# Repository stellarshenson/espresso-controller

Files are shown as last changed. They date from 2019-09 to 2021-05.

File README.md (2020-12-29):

## Homekit Enabled Rancillio Espresso Controller ##
Homekit enabled Rancilio Espresso Controller for Rancilio Silvia v5 Espresso Machine

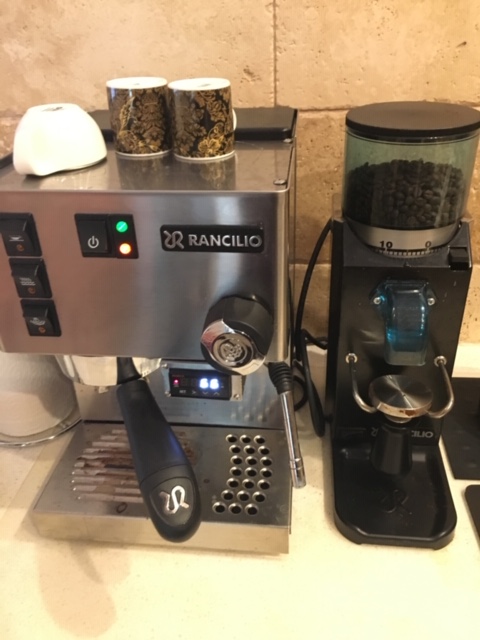
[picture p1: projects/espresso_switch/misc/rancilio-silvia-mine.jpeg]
rancilio silvia


this project was possible thanks to the freeRTOS and esp-open-sdk
Also thanks to folowing other projects:
* [maximkulkin/esp-homekit](https://github.com/maximkulkin/esp-homekit.git)
* [maximkulkin/esp-wifi-config](https://github.com/maximkulkin/esp-wifi-config)
* [ravensystem/esp-adv-button](https://github.com/RavenSystem/esp-adv-button.git)

This module is specifically designed to control turning on-and-off Rancilio Silvia v5 Espresso Machine.
Rancilio Silvia has only a momentary switch that while toggled, powers the machine on (when previously off) and off (when previously on).
Additionally Rancilio Silvia uses an internal timer that turns the machine off after 30min

Espresso Controller monitors the internal power state of the espresso machine and controls powering the machine up and down when activated

### Firmware Build ###
1. Clone the project. Next, initialize and sync all submodules (recursively):
```shell
git clone --recursive https://github.com/stellarshenson/espresso-controller.git
cd espresso-controller
git submodule update --init --recursive
```
2. Install [esp-open-sdk](https://github.com/pfalcon/esp-open-sdk), build it with `make toolchain esptool libhal STANDALONE=n`, then edit your PATH and add the generated toolchain bin directory. The path will be something like /path/to/esp-open-sdk/xtensa-lx106-elf/bin
3. Install [esptool.py](https://github.com/themadinventor/esptool) and make it available on your PATH. If you used esp-open-sdk then this is done already. Alternatively you can use the [NodeMCU flasher](https://github.com/nodemcu/nodemcu-flasher/tree/master/Win64/Release)
4. Checkout [esp-open-rtos](https://github.com/SuperHouse/esp-open-rtos) and set SDK_PATH environment variable pointing to it.
5. Build espresso_switch firmware:
```shell
make -C projects/espresso_switch suite
```
Files generated by the make script should be:
```shell
ls firmware
0x00000_rboot.bin  0x10000_blank_0x00_1M.bin  0x10000_blank_config.bin  0x20000_espresso_switch.bin
```
The prefix indicates where in the flash the firmware should be burned, use it when flashing with [esptool.py](https://github.com/themadinventor/esptool) or the [NodeMCU flasher](https://github.com/nodemcu/nodemcu-flasher/tree/master/Win64/Release). Additional settings for flashing of the firmware are: SPI Mode = DOUT, Baudrate = 230400, Flash size = <flash size of your Wemos unit in Mbyte>

### Principle of operation ###
The device is supposed to control the powering up and down the espresso machine and notify any power changes to the Homekit clients nearby. In the future the device will be able to control the auto-shutdown of the espresso machine (powersaving) and flushing (running water through the group after warm-up). Additionally the firmware will monitor the boiler temperature in the future.

Currently the device extends the following number of output interfaces:
* __Toggle interface__ - controls the toggle switch and works exactly like the momentary switch on the espresso machine front panel
* __Power sense interface__ - senses whether the machine is on or off (and provides notifications to the homekit clients)
* __Status LED__ - indicates the status of the device, fast blink = booting up, slow-blink = AP mode, no blink = connected to the network, SOS blink (3 short, 3 long, 3 short) = problem
* __Button__ - press once to manually trigger power switch (used to test device wiring). hold for 10s to reset device to factory settings

Additionally, when connected through the microUSB port to the computer, the device outputs serial diagnostics messages and extends serial commandline. Type *help* to get the list of available commands.

The serial inteface was configured with the __74880 baud rate__

### Functionality ###
Device boots up in 2 different modes:
1. as new device, you need to find its wifi ssid (Espresso-Switch-xxxx) and configure its access to your network via web captive portal
2. as connected device. you need to connect to its IP and capture its Homekit code
3. as homekit device. it is ready for operation once added to your homekit network

### Typical Circuit Layout ###
You would need the following parts to complete the build
* __Wemos D1 Mini <any>__ - any wemos with 4Mb+ flash works (Mini or Mini Pro)
* __Optocoupler + 1k Resistor (D6)__ - used for powersense. The Rancilio Silvia 12V power indicator circuit it very noisy, we would use the optocoupler to provide galvanic isolation between the controller and the espresso machine
* __Relay__ (3.3V level or Relay 5v + NPN transistor and a couple of passive jellybeans) - this needs to switch the 12v AC momentary switch
* __1 Status LED + 330 Resistor__ - this is just a status LED. Fast blink = starting up, Slow blink - AP mode, No blink - connected to network 
* __HI-Link 5V power module__ (to power the thing up from mains) - it would be preferred to connect the controller to the mains terminals at the Rancilio power brick. I am figuiring out other options, stay tuned. Voltage for the Wemos D1 must be relatively clean.Wemos has onboard a small 3v3 linear power supply controller. Please keep in mind that Wemos D1 uses 3v3 logic levels :-)

I will publish the full BOM as soon as I finish the PCB build and installation

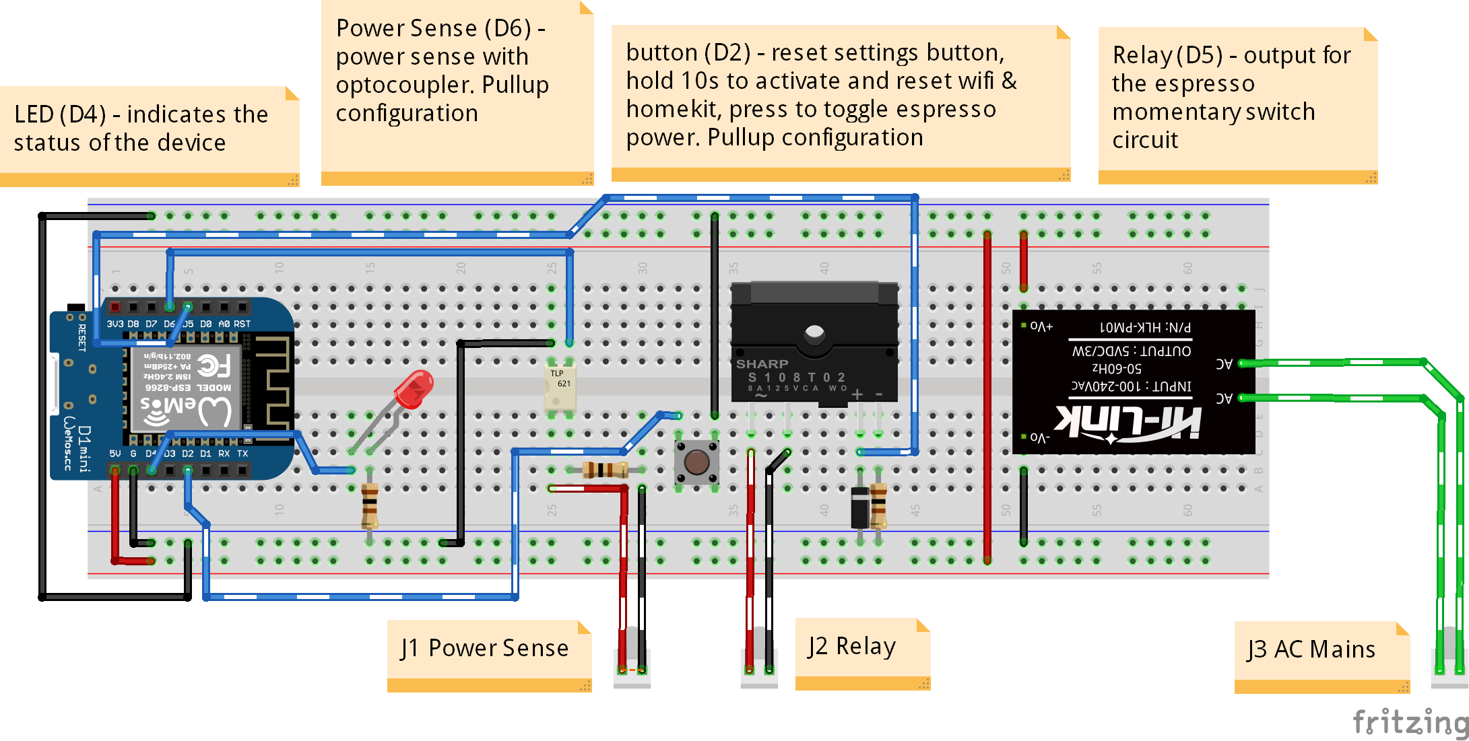
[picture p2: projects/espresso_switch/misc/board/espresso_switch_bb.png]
circuit layout

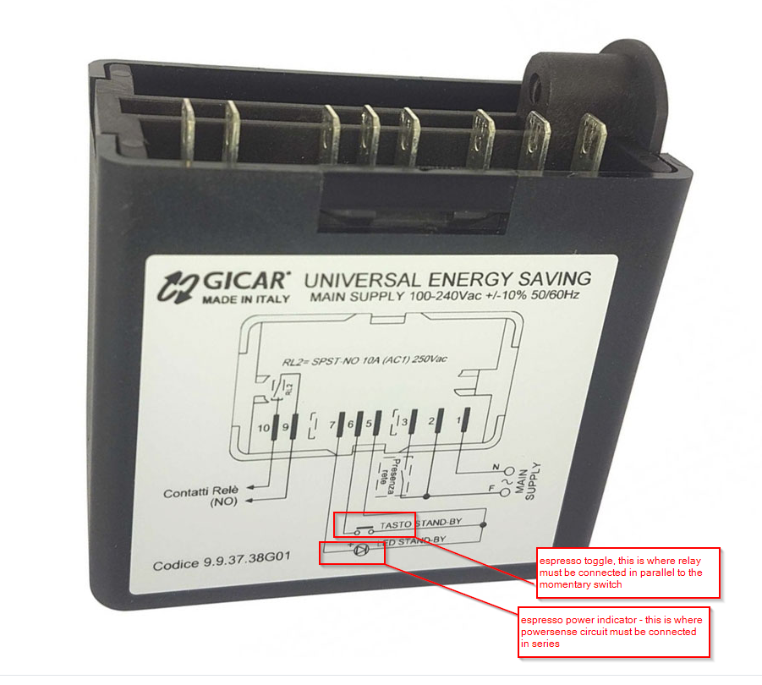
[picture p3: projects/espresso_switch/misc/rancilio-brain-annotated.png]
power brick


## Circuit and PCB ##
All schematics and PCB files are available in the [misc/board](https://github.com/stellarshenson/espresso-controller/blob/master/projects/espresso_switch/misc/board) directory. The bill of materials is up-to-date in the [schematics pdf](https://github.com/stellarshenson/espresso-controller/blob/master/projects/espresso_switch/misc/board/espresso_switch_schematics.pdf)

PCB design is for one-sided PCB with a copper pour connected to the GND. [PCB printout](https://github.com/stellarshenson/espresso-controller/blob/master/projects/espresso_switch/misc/board/espresso_switch_pcb_bottom.pdf) printout available as 600dpi to print and etch according to [instructions](https://github.com/stellarshenson/espresso-controller/blob/master/projects/espresso_switch/misc/board/pcb_howto.txt). Schematics and PCB files were produced with DipTrace

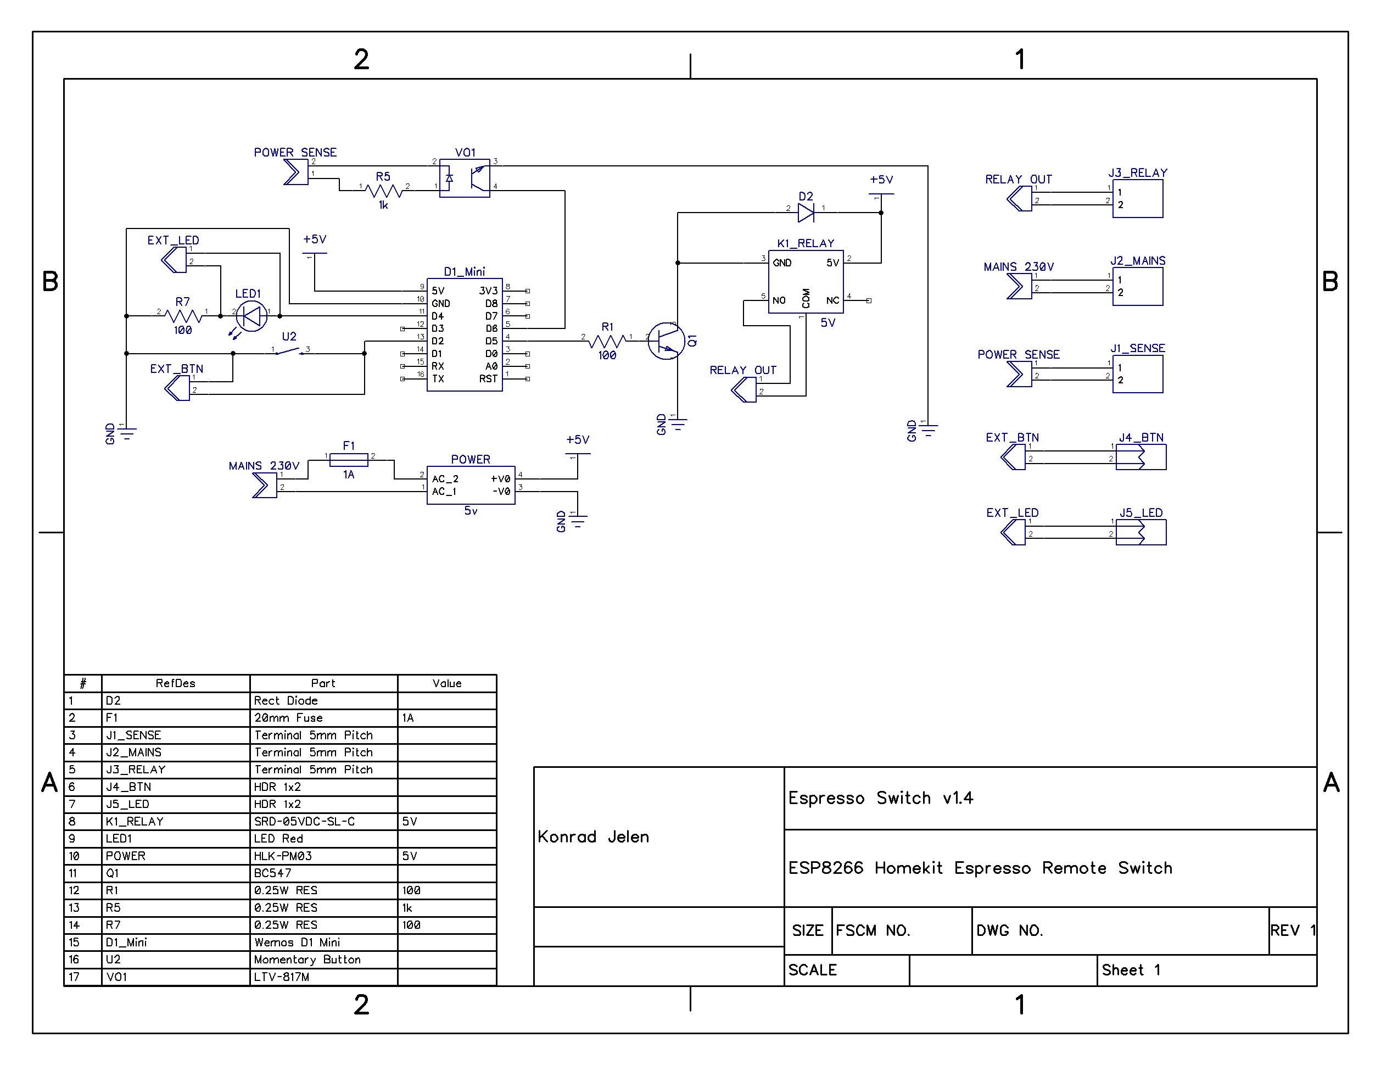
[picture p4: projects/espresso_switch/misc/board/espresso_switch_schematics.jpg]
circuit

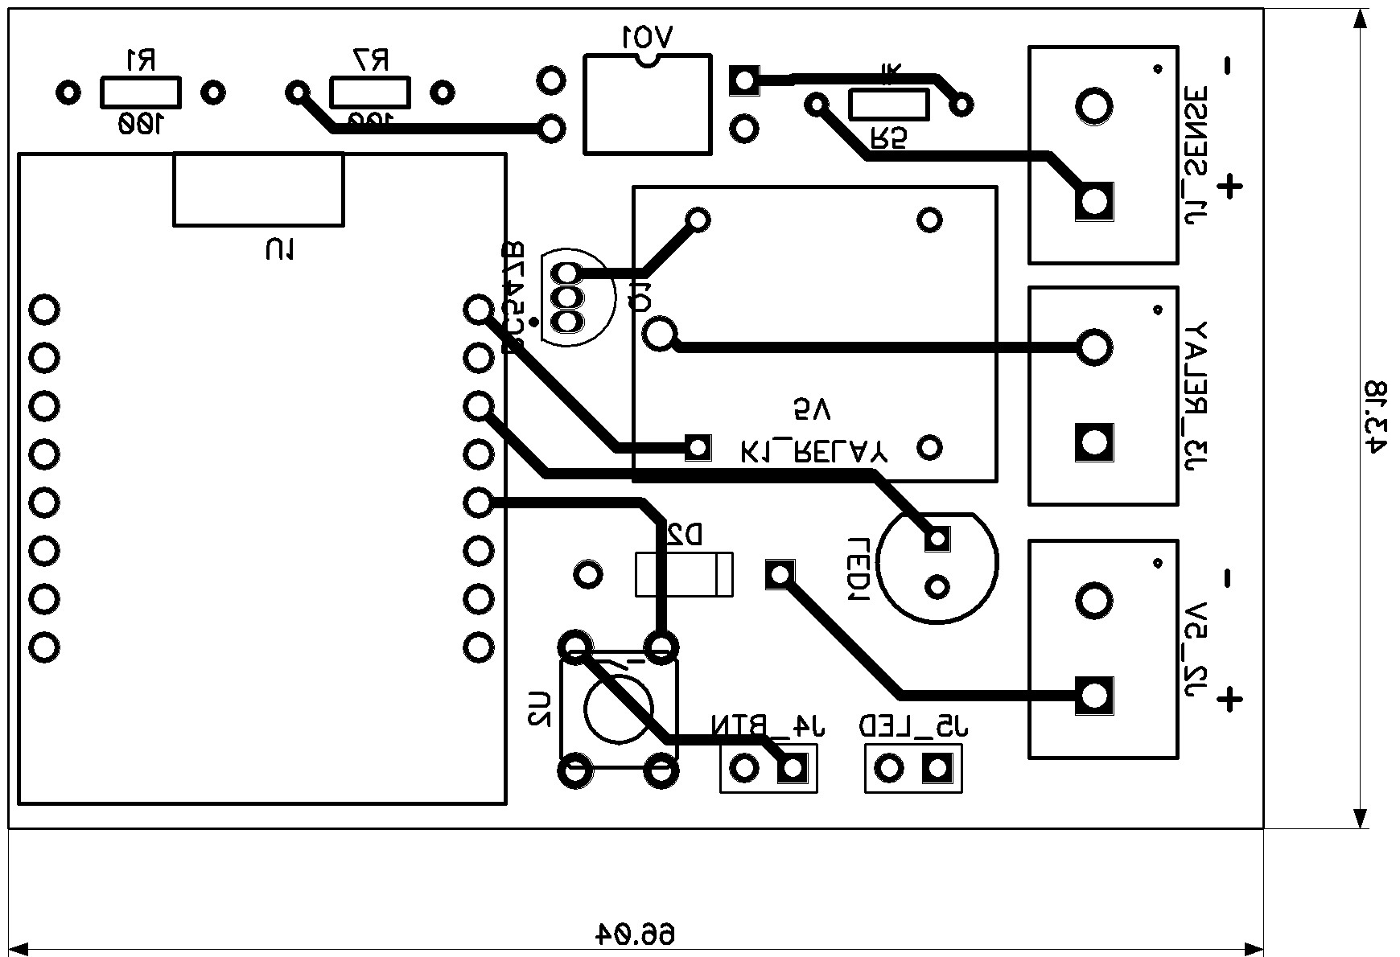
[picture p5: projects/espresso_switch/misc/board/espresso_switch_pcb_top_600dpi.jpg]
pcb top

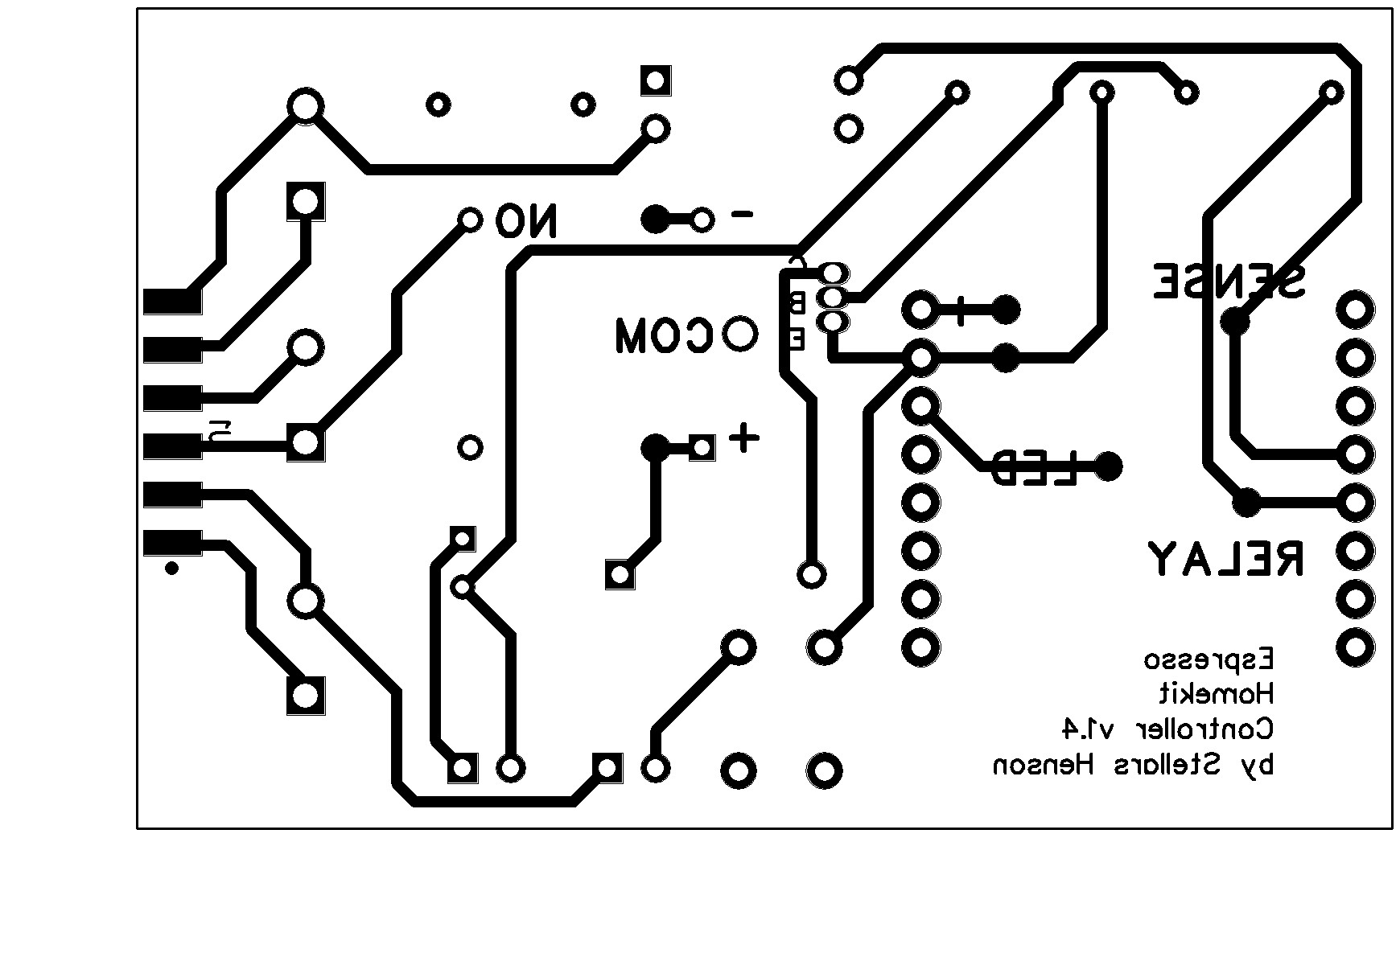
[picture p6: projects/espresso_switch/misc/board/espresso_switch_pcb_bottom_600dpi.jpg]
pcb bottom


### Installation ###
TBD

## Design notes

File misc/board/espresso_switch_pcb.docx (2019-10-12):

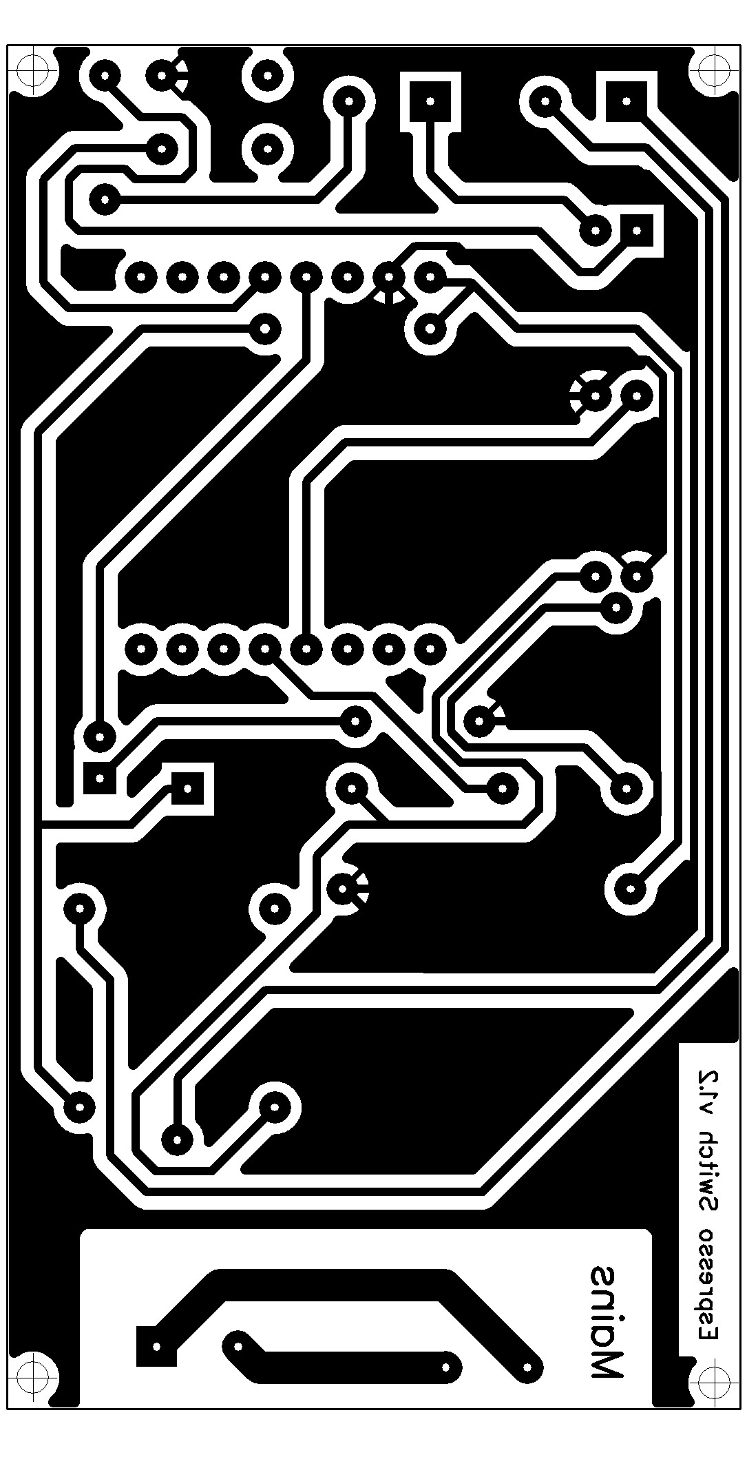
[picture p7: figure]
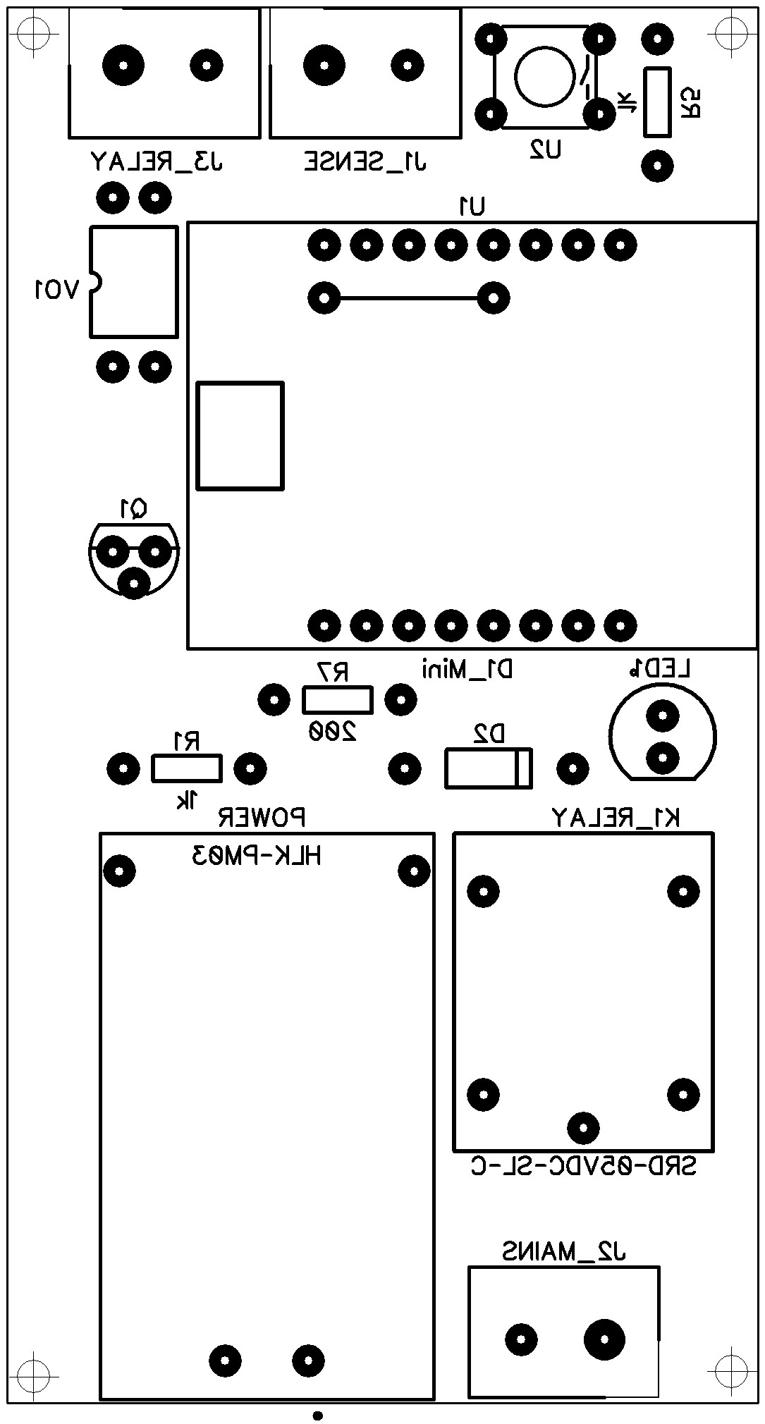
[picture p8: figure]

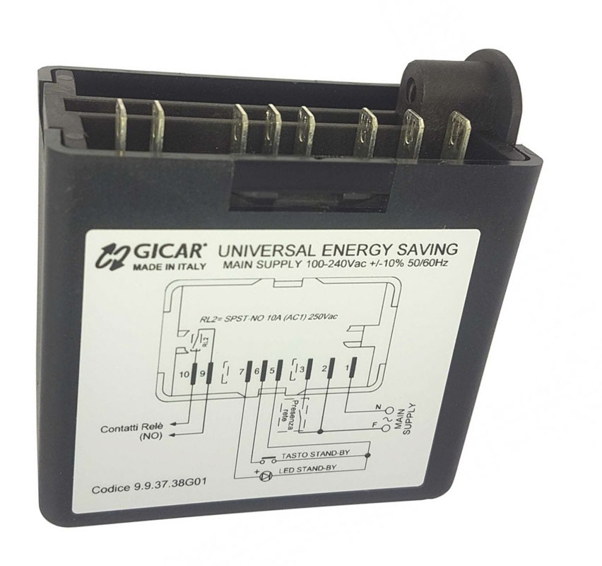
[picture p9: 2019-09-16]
misc/rancilio-brain-1.jpeg

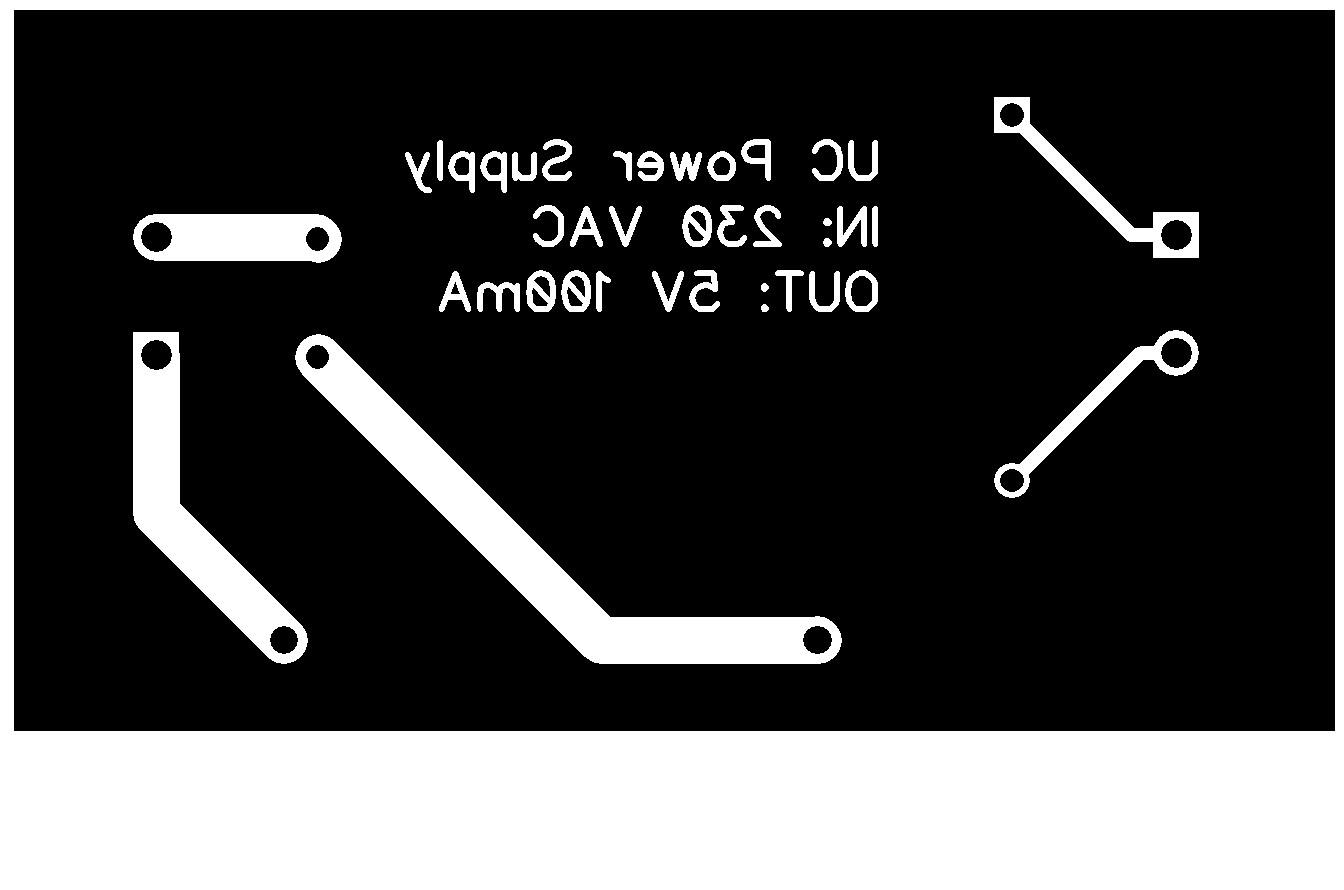
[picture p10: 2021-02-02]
misc/board/espresso_switch_power_supply_fused_bottom_600dpi.jpg

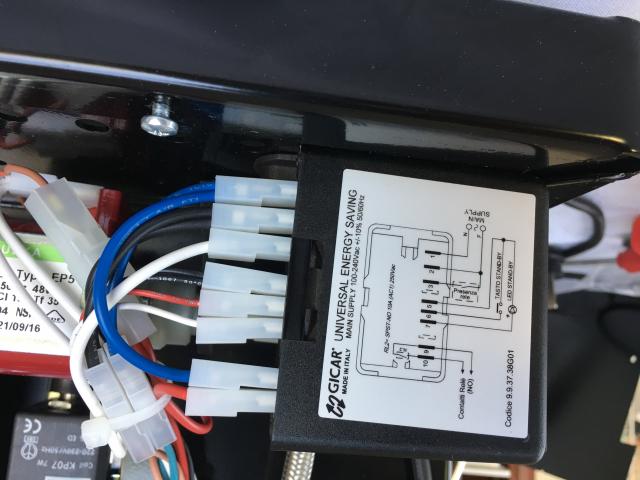
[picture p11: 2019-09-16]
misc/rancilio-brain-2.jpeg

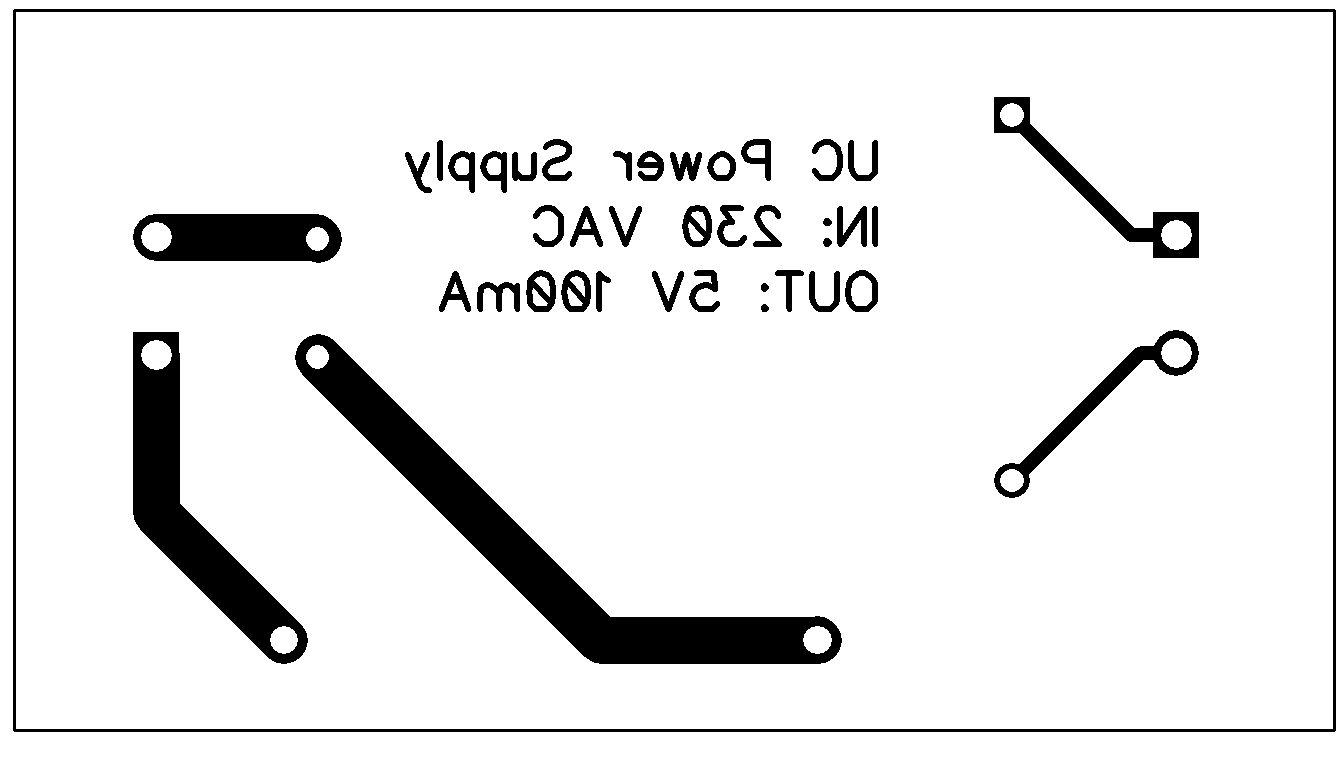
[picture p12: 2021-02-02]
misc/board/espresso_switch_pcb_bottom_600dpi.bmp

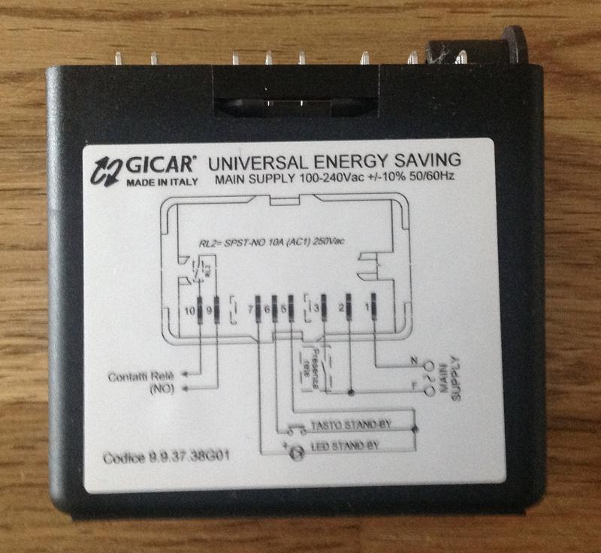
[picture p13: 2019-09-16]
misc/rancilio-brain.jpeg

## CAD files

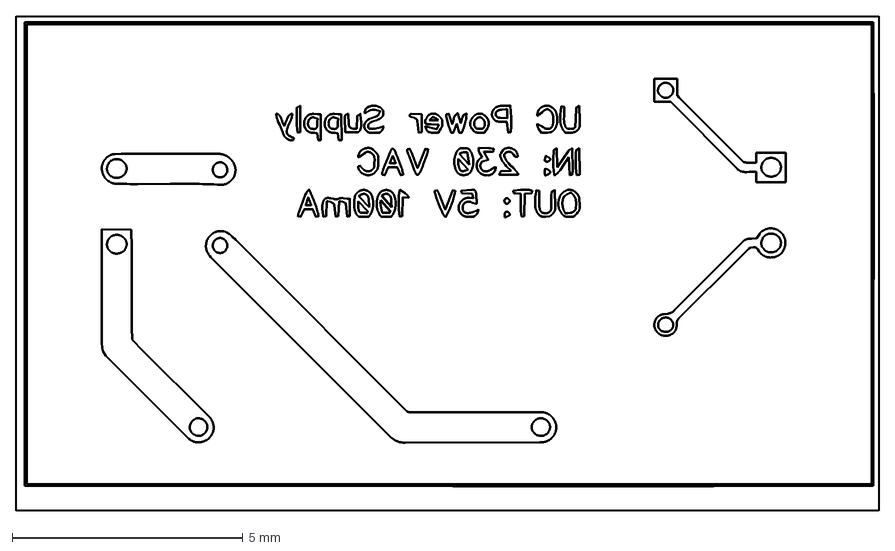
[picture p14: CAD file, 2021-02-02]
misc/board/espresso_switch_pcb_bottom_600dpi.dxf
18.7 x 10.7 mm

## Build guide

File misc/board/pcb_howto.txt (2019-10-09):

1. paste 400dpi or 600dpi bmp-s in the MS word document
2. change placement type to "background picture"
3. change picture scale to 24% (400dpi) or 16% (600dpi)

the printout should be of correct size after that

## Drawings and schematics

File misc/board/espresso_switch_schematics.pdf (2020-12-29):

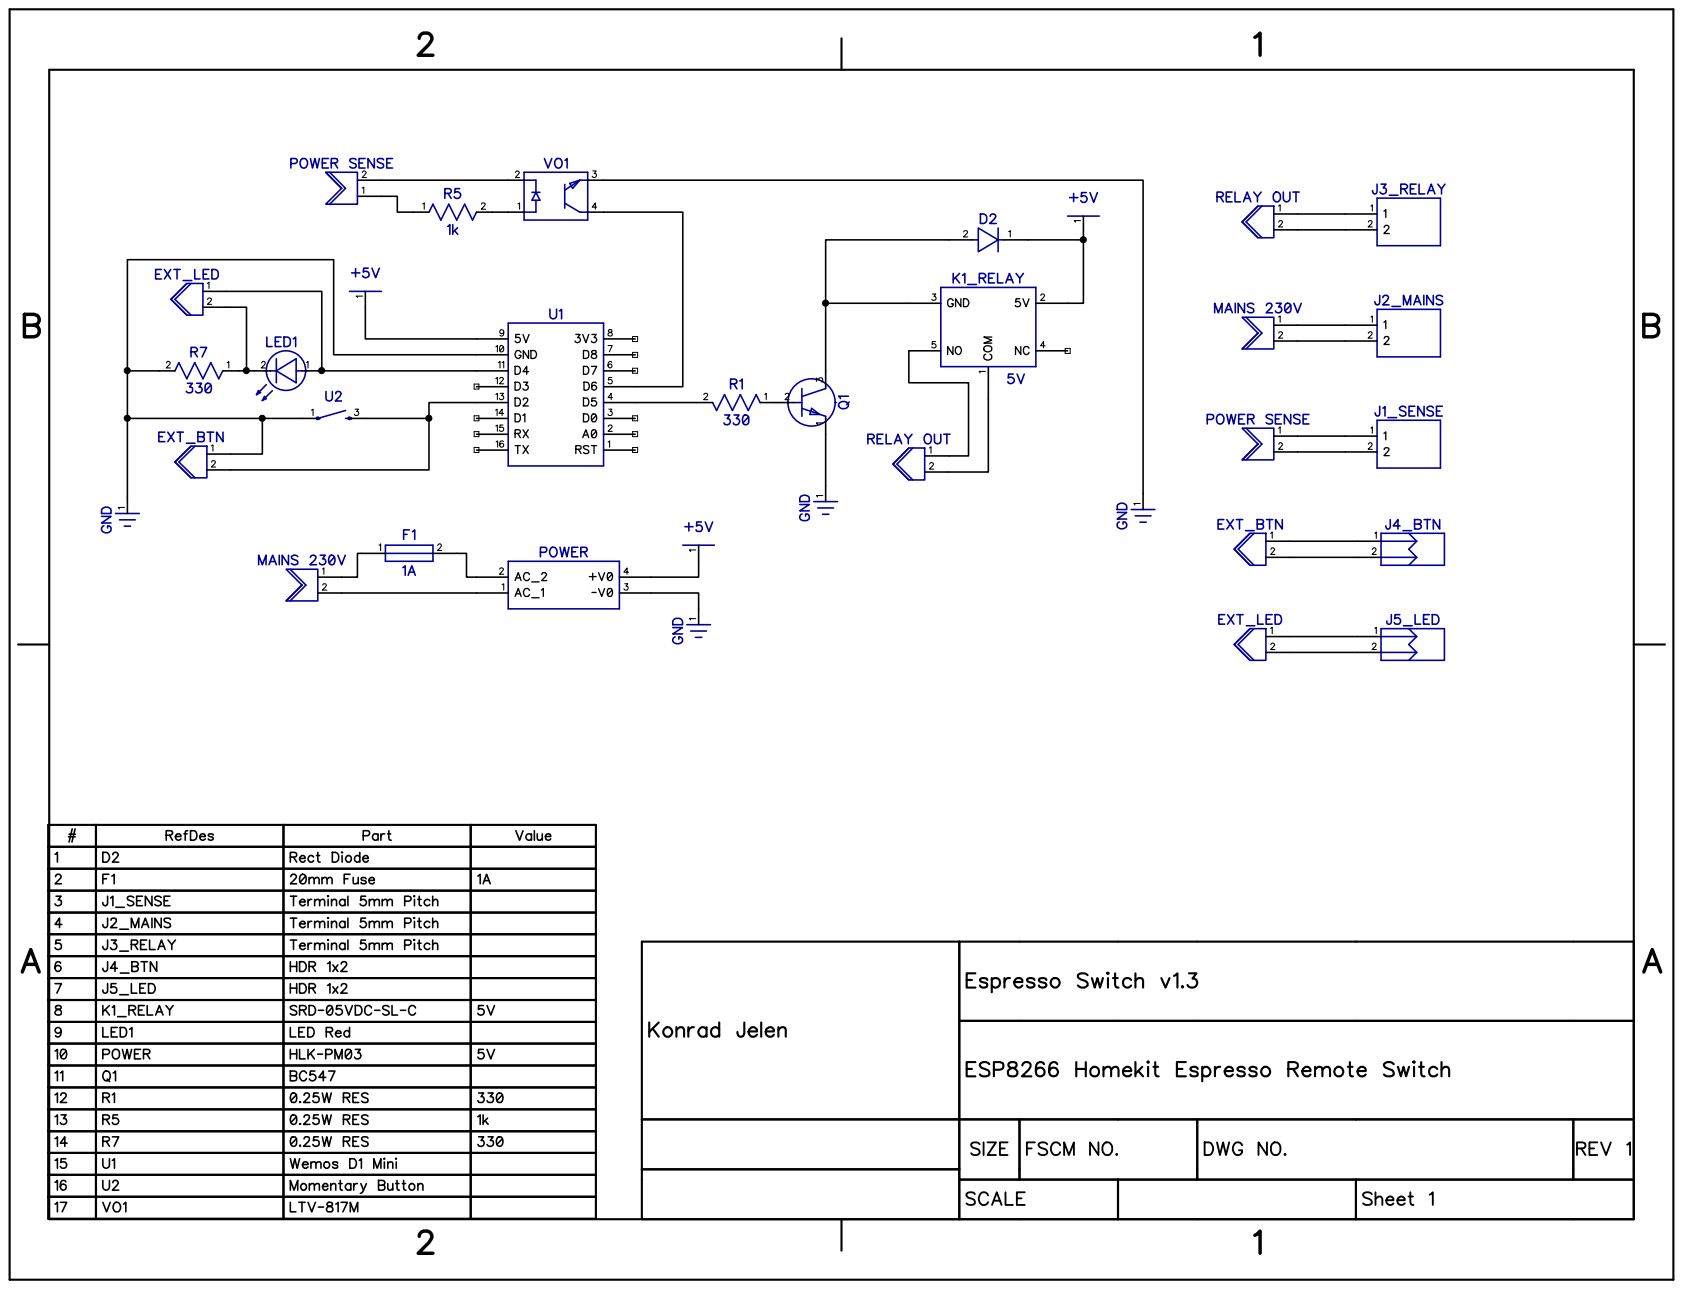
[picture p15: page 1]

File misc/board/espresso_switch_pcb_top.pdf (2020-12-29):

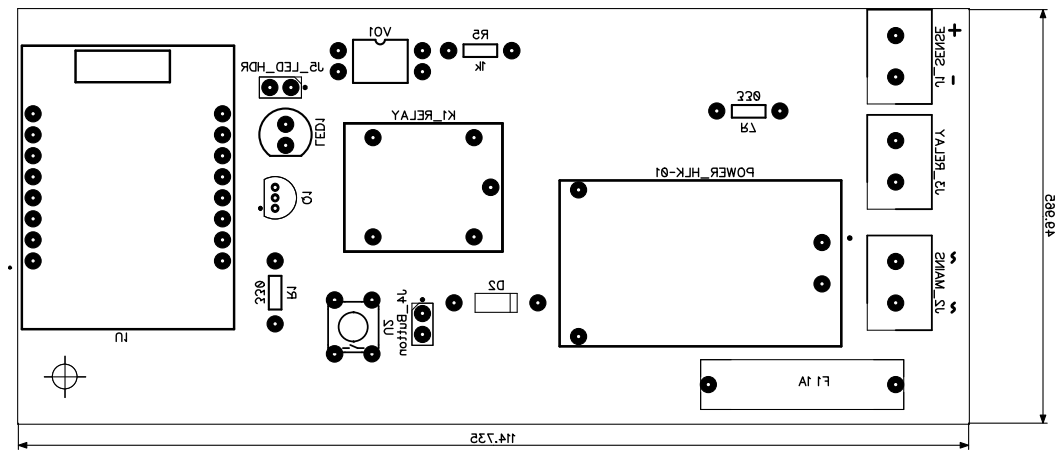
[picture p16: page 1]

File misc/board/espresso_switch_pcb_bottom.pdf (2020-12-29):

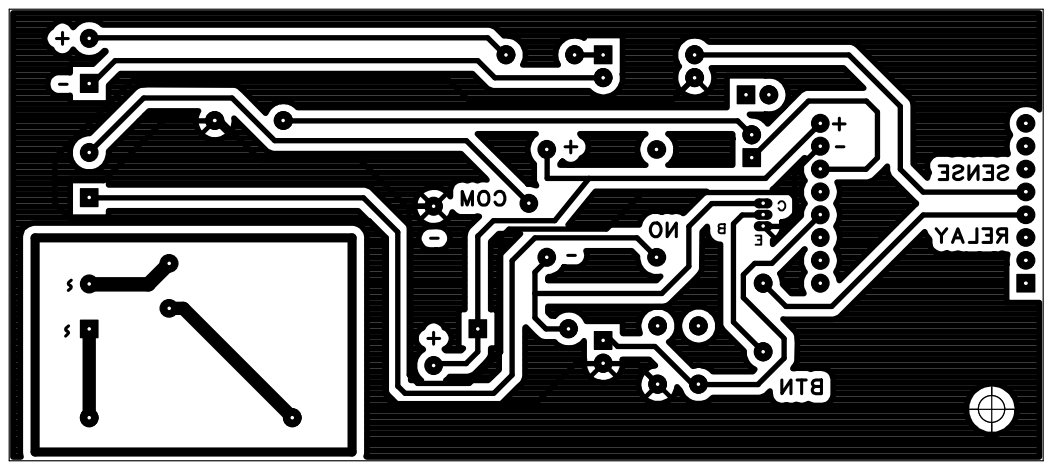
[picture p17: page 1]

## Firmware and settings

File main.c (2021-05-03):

/*
 *
 * Espresso controller accessory where On/Of functions
 * by toggling monostable switch and looks at the SENSE
 * pin to find if espresso machine is on
 *
 * This accessory uses the modified wifi-config library
 * that has the homekit id generated from the chipid and
 * starts an AP mode with a HTTP server upon start when
 * wifi config was found.
 *
 * After successful connection accessory shuts down AP.
 * 
 *  Wemos D1 Mini Pro
 *
 *                 RST -|         |- TX  / GPIO1
 *           ADC0 / A0 -|         |- RX  / GPIO3
 *  D0 / WAKE / GPIO16 -|         |- D1 / SCL / GPIO5
 *  D5 / SCLK / GPIO14 -|         |- D2 / SDA / GPIO4
 *  D6 / MISO / GPIO12 -|         |- D3 / FLASH / GPIO0
 *  D7 / MOSI / GPIO13 -|         |- D4 / GPIO2 / Onboard LED
 *  D8 / CS /   GPIO15 -|   USB   |- GND
 *                 3V3 -|___|=|___|- 5V
 */

#include <stdio.h>
#include <stdlib.h>
#include <esp/uart.h>
#include <esp8266.h>
#include <FreeRTOS.h>
#include <task.h>
#include <string.h>
#include <sysparam.h>

#include <serial-cmdline.h>
#include <led_status.h>

#include <homekit/homekit.h>
#include <homekit/characteristics.h>
#include <wifi_config.h>
#include <adv_button.h>
#include <espressif/esp_system.h>
#include <espressif/esp_common.h>
#include <esp/hwrand.h>


/* the following is for fetching the time over ntp protocol */
#include <sntp.h>
#include <time.h>

#ifndef PROTO_UUID
#define PROTO_UUID "-03a1-4971-92bf-af2b7d833922"
#endif

#ifndef UUID
#define UUID "01010101" PROTO_UUID
#endif

#define INFO(message, ...) printf(">>> " message "\n", ##__VA_ARGS__);
#define ERROR(message, ...) printf("!!! " message "\n", ##__VA_ARGS__);

#define GPIO_ESPRESSO_RELAY     14  // D5 = GPIO14
#define GPIO_STATUS_LED         2   // D3 = GPIO00, D4 = GPIO02
#define GPIO_ESPRESSO_SENSE     12  // D6 = GPIO12
#define GPIO_BUTTON             4   // D2 = GPIO04
#define ESPRESSO_SENSE_DELAY    1000
#define ESPRESSO_TOGGLE_TIME    500
#define SNTP_SYNC_PERIOD	5*60000	
#define SNTP_SERVERS		"0.pool.ntp.org", "1.pool.ntp.org", "2.pool.ntp.org", "3.pool.ntp.org"

#define DEFAULT_SWITCH_MODE	switch_mode_momentary

#define SYSPARAM_SWITCH_MODE		"switch_mode"
#define SYSPARAM_HOMEKIT_PASSWORD	"homekit_password"
#define SYSPARAM_BOOTSTRAPPED		"device_bootstrapped"


//pairing password to display, this will be embedded in the AP homepage
#define CUSTOM_HTML "<p><b>Espresso Switch Accessory </b><br> %s </p>"
#define INITIAL_ACCESSORY_PASSWORD "111-11-111"
#define HOMEKIT_SETUPID "1QJ8"

#define HOMEKIT_CUSTOM_UUID(value) (value PROTO_UUID)
#define HOMEKIT_SERVICE_CUSTOM_SETUP HOMEKIT_CUSTOM_UUID("F00000FF")
#define HOMEKIT_CHARACTERISTIC_CUSTOM_SHOW_SETUP HOMEKIT_CUSTOM_UUID("00000001")
#define HOMEKIT_DECLARE_CHARACTERISTIC_CUSTOM_SHOW_SETUP(_value, ...) \
    .type = HOMEKIT_CHARACTERISTIC_CUSTOM_SHOW_SETUP, \
    .description = "Show Setup", \
    .format = homekit_format_bool, \
    .permissions = homekit_permissions_paired_read \
    | homekit_permissions_paired_write \
    | homekit_permissions_notify, \
    .value = HOMEKIT_BOOL_(_value), \
    ##__VA_ARGS__


//prototypes
void espresso_on_callback(homekit_characteristic_t *_ch, homekit_value_t on, void *context);
void espresso_sense_task();
void espresso_toggle(bool _on);
void espresso_cycle();
void status_led_write(bool on);
void accessory_identify_task(void *_args);
void accessory_identify_callback(homekit_value_t _value);
void led_identify(homekit_value_t _value);
void show_setup_callback();
void serial_read_task();
void on_command(char* cmd);
void reset_settings();
void save_settings();
void espresso_status();

/*
 * declared characteristics:
 * espresson_on - controls espresso power
 * show_setup - controls whether custom setup visibility
 * */
homekit_characteristic_t espresso_on = HOMEKIT_CHARACTERISTIC_(ON, false, .callback=HOMEKIT_CHARACTERISTIC_CALLBACK(espresso_on_callback));
homekit_characteristic_t show_setup = HOMEKIT_CHARACTERISTIC_(CUSTOM_SHOW_SETUP, true, .callback=HOMEKIT_CHARACTERISTIC_CALLBACK(show_setup_callback));
//homekit_characteristic_t wifi_reset = HOMEKIT_CHARACTERISTIC_(CUSTOM_WIFI_RESET, false, .id=131, .callback=HOMEKIT_CHARACTERISTIC_CALLBACK(change_settings_callback));

// declare accessories / services and characteristics
// those are furhter initialised with homekit_server_init after wifi is configured
homekit_accessory_t *accessories[] = {
    //accessories
    HOMEKIT_ACCESSORY(.id=1, .category=homekit_accessory_category_lightbulb, .services=(homekit_service_t*[]){
	//servces - information
	HOMEKIT_SERVICE(ACCESSORY_INFORMATION, .characteristics=(homekit_characteristic_t*[]){
	    //characteristics
	    HOMEKIT_CHARACTERISTIC(NAME, "Espresso Switch"),
	    HOMEKIT_CHARACTERISTIC(MANUFACTURER, "Stellars"),
	    HOMEKIT_CHARACTERISTIC(SERIAL_NUMBER, "001"),
	    HOMEKIT_CHARACTERISTIC(MODEL, "Momentary Switch"),
	    HOMEKIT_CHARACTERISTIC(FIRMWARE_REVISION, "0.3"),
	    HOMEKIT_CHARACTERISTIC(IDENTIFY, accessory_identify_callback),
	    NULL
	}),
	//services - switch
	HOMEKIT_SERVICE(SWITCH, .primary=true, .characteristics=(homekit_characteristic_t*[]){
	    HOMEKIT_CHARACTERISTIC(NAME, "Espresso Switch"),
	    &espresso_on,
	    &show_setup,
	    NULL

	}),
	NULL
    }),
    NULL
};

//homekit server configuration - initial password and the list of declared accessories
homekit_server_config_t homekit_config = {
    .accessories = accessories,
    .password = "",
    .setupId = HOMEKIT_SETUPID
};

//mode of operation
typedef enum {
    switch_mode_momentary = 0,
    switch_mode_toggle = 1
} switch_mode_t;


//sense value set by the sense task
volatile homekit_value_t espresso_sense_on = { .bool_value = false }; //changed by internal sense task
volatile homekit_value_t simulate_on = { .bool_value = false }; //changed by commands
volatile bool simulation_enabled = false;  //when true, status is read only from commands until next reboot
volatile bool led_status = false; //led status, need for reporting status
volatile int8_t switch_mode = (int8_t) DEFAULT_SWITCH_MODE; //momentary by default (we save it anyway) 


/**
 * espresso callback function to receive value and enable the toggle
 * when callback was initated by the sense task - no action is taken
 * */
void espresso_on_callback(homekit_characteristic_t *_ch, homekit_value_t _on, void *_context) {
    switch(switch_mode) {
	//when toggle mode, flip the switch on or off, no matter the power state
	case switch_mode_toggle:
	    espresso_toggle(_on.bool_value);
	    break;
	//when momentary mode, cycle the switch. Mind that this event is called also by the sense task
	case switch_mode_momentary:
	    //called from cycling the switch manually (button, homekit or command)
	    if(espresso_sense_on.bool_value != _on.bool_value) 
		espresso_cycle();
	    break;
	default:
	    break;
    }
}

/**
 * cycle the momentary switch turning it on-and-off, this is used only in "momentary" mode
 * here we do not change the espresso_on value, we let sense mechanism to set the value
 * */
void espresso_cycle() {
    INFO("espresso_switch: <cycle momentary switch> current power status is: %s", espresso_sense_on.bool_value ? "on" : "off");
    gpio_write(GPIO_ESPRESSO_RELAY, 1);
    status_led_write(1);
    vTaskDelay(ESPRESSO_TOGGLE_TIME / portTICK_PERIOD_MS);
    gpio_write(GPIO_ESPRESSO_RELAY, 0);
    status_led_write(0);
}

/**
 * flip the switch to either on or off, this is used only in the "toggle" mode
 * */
void espresso_toggle(bool _on) {
    INFO("espresso_switch: <toggle switch> setting state = %s", _on ? "on" : "off" );
    gpio_write(GPIO_ESPRESSO_RELAY, _on);
    espresso_on.value.bool_value = _on;
    status_led_write(_on);
}

/***
 * change status of espresso switch from current to opposite
 * by either flipping the toggle or executing momentary 
 * */
void espresso_switch() {
	if (switch_mode == switch_mode_toggle)
	    espresso_toggle(espresso_on.value.bool_value ? 0 : 1);
	else
	    espresso_cycle();
}


/**
 * LED status light
 * */
void status_led_write(bool _on) {
    led_status = _on;
    gpio_write(GPIO_STATUS_LED, _on ? 1 : 0);
}

/**
 * monitor the status of espresso power
 * run this in a loop, find if the sense pin changed state
 * */
void espresso_sense_task() {
    //this is used to detect changes to the power status
    homekit_value_t previous_espresso_sense_on = { .bool_value = espresso_sense_on.bool_value };

    //keep monitoring by going idle for a predefined time and then sense again.
    //when status of the espresso changed - notify homekit
    while(1) {
    	vTaskDelay(ESPRESSO_SENSE_DELAY / portTICK_PERIOD_MS);

        //by default read status from GPIO_ESPRESSO_SENSE. Otherwise read from simulation
	//sense gpio has pullup enabled and shorts to the GND when power is on
    	if(! simulation_enabled) espresso_sense_on.bool_value = ! gpio_read(GPIO_ESPRESSO_SENSE);
    	else espresso_sense_on.bool_value = simulate_on.bool_value; //read simulation value

	//detect changes to the power from previous and synchronise
	if (previous_espresso_sense_on.bool_value != espresso_sense_on.bool_value) {
	    INFO("espresso_switch: <sense> power status changed %s->%s", 
		   previous_espresso_sense_on.bool_value ? "on" : "off", espresso_sense_on.bool_value ? "on" : "off");
	    previous_espresso_sense_on.bool_value = espresso_sense_on.bool_value;
	}

	//ignore notifications about power state change when mode == toggle
    //make sure LED indicates power status but only in momentary mode
	if (switch_mode == switch_mode_toggle) continue;
	else status_led_write(espresso_sense_on.bool_value);

	//when internal state different from homekit state - notify
	//also change the status value  of the espresso 
    	if (espresso_sense_on.bool_value != espresso_on.value.bool_value) {
	    //notify homekit, but this event is going to be ignored by espresso_on_callback
	    INFO("espresso_switch: <sense> power status is now = %s", espresso_sense_on.bool_value ? "on" : "off");
	    espresso_on.value.bool_value = espresso_sense_on.bool_value;
	    homekit_characteristic_notify(&espresso_on, espresso_sense_on);
    	}
    }

    vTaskDelete(NULL);
}

/**
 * identify accessort
 * */
void accessory_identify_callback(homekit_value_t _value) {
    INFO("espresso_switch: identify accessory");
    xTaskCreate(accessory_identify_task, "Accessory identify", 128, NULL, 2, NULL);
}

/**
 * show setup in the configuration app (eve)
 * */
void show_setup_callback() {
   save_settings();
}



/**
 * task run to identify the accessory
 * */
void accessory_identify_task(void *_args) {
   for (int i=0; i<3; i++) {
        for (int j=0; j<2; j++) {
            status_led_write(true);
            vTaskDelay(100 / portTICK_PERIOD_MS);
             status_led_write(false);
            vTaskDelay(100 / portTICK_PERIOD_MS);
       }

       vTaskDelay(250 / portTICK_PERIOD_MS);
   }

    vTaskDelete(NULL);
}

/**
 * taks to connect to NTP servers and get current time
 * SNTP initiation conflicts with mDNS, make sure this 
 * task is created only after homekit was started
 * */
void sntp_task(void *_args)
{
	const char *servers[] = {SNTP_SERVERS};

	/* Start SNTP */
	INFO("Starting SNTP... ");
	/* SNTP will request an update each SNTP_SYNC_PERIOD miliseconds  */
	sntp_set_update_delay(SNTP_SYNC_PERIOD);
	/* Set UTC zone, daylight savings off */
	const struct timezone tz = {0*60, 0};
	/* SNTP initialization */
	sntp_initialize(&tz);
	/* Servers must be configured right after initialization */
	sntp_set_servers(servers, sizeof(servers) / sizeof(char*));
	INFO("SNTP connection established");

	/* Print date and time and exit */
	vTaskDelay(5000 / portTICK_PERIOD_MS);
	time_t ts = time(NULL);
	printf("SYSTEM UTC TIME: %s", ctime(&ts));

	vTaskDelete(NULL);
}

/**
* callbck function for the holdpress on GPIO_BUTTON
*/
void on_button_holdpress_callback(uint8_t gpio, void* context) {
    INFO("espresso_switch: <button> registered holdpress on pin: %u", gpio);
    reset_settings();
}

/**
* callbck function for singlepress on GPIO_BUTTON
*/
void on_button_singlepress_callback(uint8_t gpio, void* context) {
    INFO("espresso_switch: <button> registered singlepress on pin: %u", gpio);
    espresso_switch();
}


/**
 * process commands
 * */
void on_command_callback(char* cmdline) {
    static char cmd_buffer[192];
    char *cmd = &cmd_buffer[0];
    char *arg1 = &cmd_buffer[64];
    char *arg2 = &cmd_buffer[128];

    //fill in arguments, apply safety
    sscanf(cmdline, "%63s %63s %63s", cmd, arg1, arg2);

    if(!strcmp(cmd, "reset")) {
	reset_settings();
    } else if (!strcmp(cmd, "setup_accessory")) {
	   INFO("espresso_switch: setting up accessory with the: %s", cmdline );
	   
       if (!strcmp(arg1,"mode") && !strcmp(arg2, "toggle")) {
	       INFO("espresso_switch: changing switch mode to %s", arg2 );
	       switch_mode = switch_mode_toggle;
	       save_settings();
        } else if (!strcmp(arg1,"mode") && !strcmp(arg2,"momentary")) {
	       INFO("espresso_switch: changing switch mode to %s", arg2 );
	       switch_mode = switch_mode_momentary;
	       save_settings();
        }
    } else if (!strcmp(cmd, "setup_wifi")) {
        INFO("espresso_switch: setting up wifi with the: %s", cmdline );
        wifi_config_set(arg1, arg2);
        wifi_config_get(&arg1, &arg2);
        INFO("espresso_switch: ssid = '%s', password = '%s', restarting...", arg1, arg2);
        sdk_system_restart();
    } else if (!strcmp(cmd, "info_accessory")) {
        INFO("espresso_switch: info about the accessory, password: %s, mode: %s", homekit_config.password, switch_mode == switch_mode_momentary ? "momentary" : "toggle" );
    } else if (!strcmp(cmd, "info_wifi")) {
        INFO("espresso_switch: getting information about wifi connection");
        wifi_config_get(&arg1, &arg2);
        INFO("espresso_switch: ssid = '%s', password = '%s'", arg1, arg2);
    } else if( !strcmp(cmd, "reset_wifi") ) {
        INFO("espresso_switch: resetting wifi settings");
    	wifi_config_reset();
    	sdk_system_restart();
    } else if( !strcmp(cmd, "reset_accessory") ) {
    	INFO("espresso_switch: resetting accessory pairing and settings");
    	homekit_server_reset();
    	sdk_system_restart();
    } else if( !strcmp(cmd, "reboot") ) {
    	INFO("espresso_switch: rebooting");
    	sdk_system_restart();
    } else if( !strcmp(cmd, "simulate_on") ) {
    	INFO("espresso_switch: Simulating espresso internal on");
    	simulation_enabled = true;
    	simulate_on.bool_value = true;
    } else if( !strcmp(cmd, "simulate_off") ) {
    	INFO("espresso_switch: Simulating espresso internal off");
    	simulation_enabled = true;
    	simulate_on.bool_value = false;
    } else if( !strcmp(cmd, "simulation_disable") ) {
    	INFO("espresso_switch: Disabling simulation");
    	simulation_enabled = false;
    } else if( !strcmp(cmd, "switch") ) {
    	INFO("espresso_switch: activate the switch");
    	simulation_enabled = false;
        espresso_switch();
    } else if( !strcmp(cmd, "status") ) {
        INFO("espresso_switch: espresso machine status: %s", espresso_sense_on.bool_value ? "on" : "off");
        espresso_status();
    } else if( !strcmp(cmd, "time") ) {
    	INFO("espresso_switch: reporting time of day");
    	time_t ts = time(NULL);
	printf("SYSTEM UTC TIME: %s", ctime(&ts));
    } else if( !strcmp(cmd, "help") ) {
    	INFO("espresso_switch: Available commands:\n\
    reboot - reboots the device, no changes to the settings\n\
    setup_wifi <ssid> <password> - sets wifi ssid and passwords and reboots \n\
    setup_accessory mode [momentary|toggle] - sets switch operation mode\n\
    info_accessory - provides information about current accessory setup \n\
    info_wifi - provides information about current wifi connction \n\
    reset - resets the device settings to factory\n\
    reset_accessory - resets pairing and accessory information and restarts homekit server\n\
    reset_wifi - resets wifi ssid and password and reboots\n\
    switch - turns the espresso machine on or off\n\
    simulate_on - simulates espresso power status on\n\
    simulate_off - simulates espresso power status off\n\
    simulation_disable - disable simulation\n\
    time - report current system time\n\
    status - returns the status of the espresso power circuit\n");
    }
}

/**
callback for events emitted by the homekit
currently serve only to start SNTP only when homekit was activated
 * */
void on_homekit_event_callback(homekit_event_t _event) {
    if (_event == HOMEKIT_EVENT_SERVER_INITIALIZED) {
    	//wait a little for mDNS to activate
        vTaskDelay(3000 / portTICK_PERIOD_MS);

    	//start time SNTP client
    	xTaskCreate(sntp_task, "SNTP", 1024, NULL, 1, NULL);	
    }
}

/**
 * called when wifi configuration was completed
 * this function starts the homekit server
 * */
void on_wifi_event_callback(wifi_config_event_t _event) {
    //when connected to network register homekit event handler 
    //and start homekit server
    if (_event == WIFI_CONFIG_CONNECTED && sdk_wifi_get_opmode() != STATION_MODE) {
    	INFO("espresso_switch: connected to the network");
    	INFO("espresso_switch: starting homekit server");
    	homekit_config.on_event = on_homekit_event_callback;
    	homekit_server_init(&homekit_config);
    }

    //when in AP mode, simply drive the status LED to indicate
    if (_event == WIFI_CONFIG_CONNECTED && sdk_wifi_get_opmode() != STATIONAP_MODE) {
    	INFO("espresso_switch: running in AP mode");
    	INFO("espresso_switch: starting homekit server");
    	homekit_config.on_event = on_homekit_event_callback;
    	homekit_server_init(&homekit_config);
    }
}


/**
 * generates accessory password from the chip_id, turns 32 bit chipID into 4-bit chunks and gets modulo 9 from each
 * and generates the custom section to be displayed with the wifi_config AP server
 * */
void homekit_password_init() {

    //generate random password and write to sysparams if no password yet
    //we initialise password with empty string, so it never is NULL
    if (homekit_config.password[0] ==0) {
        uint32_t chipId = sdk_system_get_chip_id();
        INFO("espresso_switch: no password available, generating new one from chip ID: %d", chipId);
        uint8_t homekit_password[] = { chipId %10,(chipId>>1) %10,(chipId >>2) %10,(chipId >>3) %10,(chipId >>4) %10,(chipId >>5) %10, (chipId >>6) %10,(chipId >>7) %10};
        homekit_config.password = (char*) calloc( 12 , sizeof(char));

      	//write accessory password and save it
      	snprintf(homekit_config.password, 11, "%u%u%u-%u%u-%u%u%u", homekit_password[0],homekit_password[1],homekit_password[2],homekit_password[3],
	    homekit_password[4],homekit_password[5],homekit_password[6],homekit_password[7]);

        INFO("espresso_switch: setting homekit password = %s", homekit_config.password);

        //save new password
        save_settings();
    }

    //write custom section with the password
    INFO("espresso_switch: accessory password: %s", homekit_config.password);
    char *buffer = (char*) calloc(strlen(homekit_config.password) + strlen(CUSTOM_HTML), sizeof(char));
    snprintf(buffer, strlen(homekit_config.password) + strlen(CUSTOM_HTML) + 1, CUSTOM_HTML, homekit_config.password);

    //set custom section. This is used in the wifi-config library
    wifi_config_set_custom_html(buffer);
}

/**
 * initialises button and button taks
 */
void button_init() {
    adv_button_set_evaluate_delay(10);
    adv_button_create(GPIO_BUTTON, true, false);
    adv_button_register_callback_fn(GPIO_BUTTON , on_button_holdpress_callback, button_event_type_holdpress, NULL);
    adv_button_register_callback_fn(GPIO_BUTTON , on_button_singlepress_callback, button_event_type_singlepress, NULL);

    INFO("espresso_switch: initialised hold-press button on pin: %d", GPIO_BUTTON);
}


/**
 * initialises the espresso state sense and prepare the toggle
 * this function launches the perpetual task to check the status of
 * of the espresso circuit and notifiy homekit on the status change
 * */
void espresso_init() {
    //enable ESPRESSO_RELAY pin for OUTPUT and ESPRESSO_SENSE for INPUT
    gpio_enable(GPIO_ESPRESSO_RELAY, GPIO_OUTPUT);
    gpio_enable(GPIO_STATUS_LED, GPIO_OUTPUT);
    gpio_enable(GPIO_ESPRESSO_SENSE, GPIO_INPUT);
    gpio_set_pullup(GPIO_ESPRESSO_RELAY, false, false);
    gpio_set_pullup(GPIO_ESPRESSO_SENSE, true, true);
    gpio_write(GPIO_ESPRESSO_RELAY, 0); //turn off the relay
    status_led_write(false);

    //report status to stdout
    espresso_status();

    //enable sense task
    xTaskCreate(espresso_sense_task, "Espresso Sense", 512, NULL, 1, NULL);
}

/**
 * reports espresso status to the stdout
 * */
void espresso_status() {
    uint32_t chipId = sdk_system_get_chip_id();
    INFO("espresso_switch: chipId = %d", chipId);
    INFO("espresso_switch: switch status: %s, power status: %s", espresso_on.value.bool_value ? "on" : "off", espresso_sense_on.bool_value ? "on" : "off");
    INFO("espresso_switch: espresso relay on gpio = %u, sense on gpio = %u and status led gpio = %u", GPIO_ESPRESSO_RELAY, GPIO_ESPRESSO_SENSE, GPIO_STATUS_LED);
    INFO("espresso_switch: accessory password = '%s' setupId = %s, mode = %s", homekit_config.password, homekit_config.setupId, switch_mode == switch_mode_momentary ? "momentary" : "toggle");
    INFO("espresso_switch: status led = %s", led_status ? "enabled" : "disabled");
    INFO("espresso_switch: simulation = %s", simulation_enabled ? "enabled" : "disabled");

}
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

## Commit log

2019-09-06 implemented sense timer and espresso status sense
2019-09-07 added button
2019-09-10 implmented stable uart command scanning
2019-09-10 added help line for reboot command
    [main.c]
2019-09-10 updated with new prototype for the custom_html_section
2019-09-10 updated with externalised commandline driver
2019-09-10 implemented commandline driver library
2019-09-12 fixed commandline listener and its uise in the accessory
    [main.c]
2019-09-14 removed old button implementation, taken ravencore's implementation
2019-09-14 implemented hold button event
2019-09-14 reverted the origing for adv button
2019-09-15 added fritzig files - the circuit model
    [espresso_switch.fzz]
2019-09-15 updated to have toggle control on pin 14
2019-09-15 implemented reset on button hold, toggl;e on singlepress
    [espresso_switch.fzz]
2019-09-15 updated schematics
    [espresso_switch.fzz]
2019-09-15 added remaining schematics files
2019-09-15 updated schematics and the readme file with the schematics
    [espresso_switch.fzz]
2019-09-16 updated to point at the circuit layout
2019-09-16 updated to show annotated power brick
2019-09-16 added note about the bill-of-materials
2019-09-16 updated breadboard circuit layout
    [espresso_switch.fzz]
2019-09-16 updated schematics with the Hi-Link power module
    [espresso_switch.fzz]
2019-09-16 fixed schematics power sense wiring
    [espresso_switch.fzz]
2019-09-16 updated wiring
    [espresso_switch.fzz]
2019-09-17 switched to v2 of the esp-wifi-config library with new event handling
2019-09-17 updated schematics and the picture with the npn driver transistor
    [espresso_switch.fzz]
2019-09-19 updated schematics with npn transistor
    [espresso_switch.fzz]
2019-09-20 added diptrace schematics file
2019-09-20 added schematics files
    [espresso-switch-eagle.sch, espresso-switch.brd, espresso-switch.sch]
2019-09-21 removed pulldown from button, added schematics
    [espresso_switch.fzz]
2019-09-21 created schematics and the pcb
    [espresso-switch-eagle.sch, espresso-switch.brd, espresso-switch.sch]
2019-09-22 updated schematics with the BOM
2019-09-22 updated BOM
2019-09-22 added printouts of the PCB
2019-09-22 updated readme with pcb printouts
2019-09-22 updated pcb footprint to make it smaller
2019-09-22 updated schematics and the pcb with new layout and standoff for mains
2019-09-22 changed name of the switch pin to relay pin, enabled sense pullup
2019-09-22 updated pcb to change pad sizes for easy drilling
2019-09-22 updaded pcb layout
2019-09-26 renamed file and updated pcb with keepouts
2019-10-02 reduced pcb footprint and replaced hlk_pm05 with hlk_pm03
2019-10-02 updated pdf printouts scale
2019-10-03 made slim version of the board
2019-10-03 renamed board files and moved to board folder
    [espresso_switch.fzz]
2019-10-04 moved files to a modified directory structure
    [espresso_switch.fzz]
2019-10-04 added updated schematics
2019-10-04 added titles to the schematics
2019-10-04 updated schematics BOM
2019-10-04 added pcb howto instructions
2019-10-09 updated schematics with new patterns
2019-10-09 added printouts
2019-10-10 made slimmer outline by 1cm
2019-10-10 shaved vertical size by 1mm
2019-10-10 updated board size and traces layout
2019-10-10 updated with new relay circuit from npn transistor
2019-10-10 updated schematic printout
2019-10-10 updated schematics with new refdefs
2019-10-10 changed status led pin to D3 (GPIO0)
2019-10-10 fixed led initialisation
2019-10-10 added wemos schematics
2019-10-11 updated schematics with correct relay circuit (in progress)
2019-10-11 re-routed relay circuitry
2019-10-11 renamed design to 1.2 and shaved 2mm of the board height
2019-10-11 updated mirroring of the board overview
2019-10-11 removed unnecessary resistor and reduced board footprint
2019-10-12 updated pcb printout
2020-12-26 updated diagram
    [espresso_switch.fzz]
2020-12-26 updated board and schematics
    [espresso_switch.fzz]
2020-12-26 updated board
2020-12-26 updated LED placement
2020-12-26 returned to having diode with the relay
2020-12-26 thickened mains traces
2020-12-27 updated traces
2020-12-27 updated breadboard
    [espresso_switch.fzz]
2020-12-27 updated traces layout
2020-12-28 updated the board
2020-12-29 added production board and firmware files
2020-12-29 added fuse
2020-12-29 base resistor value
2020-12-30 added separate power supply
2020-12-30 added fused ps
2021-02-02 updated files
    [espresso_switch_pcb_bottom_600dpi.dxf]
2021-02-02 updated fuse
2021-05-08 simplifield build
    [espresso_switch.fzz, espresso_switch_pcb_bottom_600dpi.dxf]
